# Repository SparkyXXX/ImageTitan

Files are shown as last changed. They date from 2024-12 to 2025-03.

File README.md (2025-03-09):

# 环视采图车使用说明

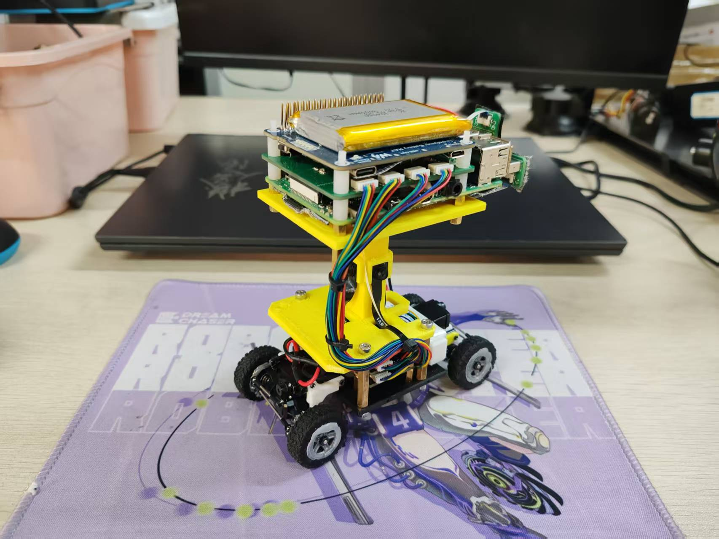
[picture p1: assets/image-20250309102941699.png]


图采车配合手柄、无线键鼠（其实无线键盘就可以）和显示器使用，前者用于操控小车，后者用于启动程序或调试处理异常状况。（如果希望更方便一些省去键鼠也可以在ubuntu上配置自启动）

## 使用步骤

1. 给树莓派插入无线键鼠和手柄的USB接收端，连接好显示器，将手柄开机。

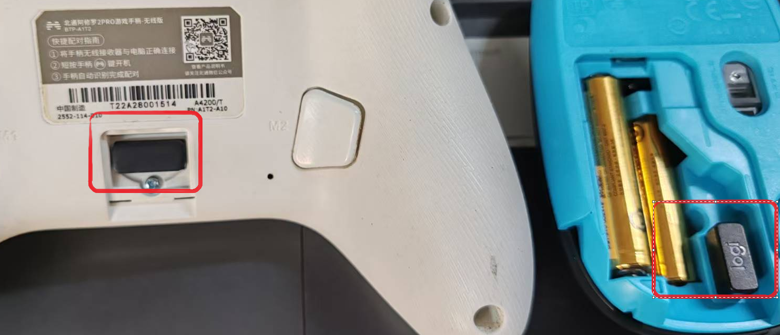
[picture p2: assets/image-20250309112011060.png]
    

2. 按此按钮给树莓派上电

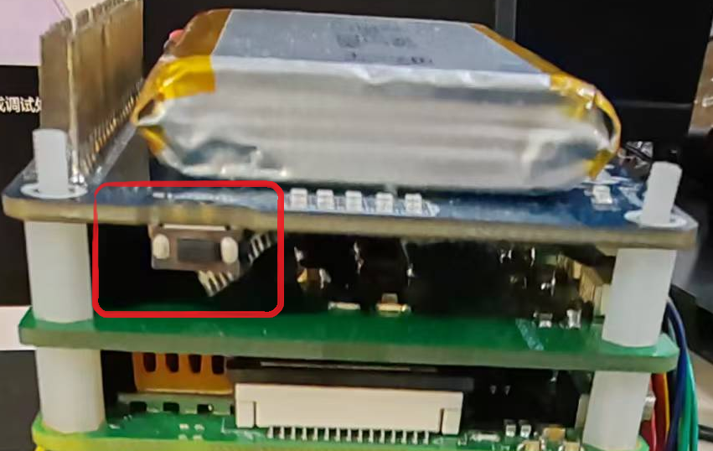
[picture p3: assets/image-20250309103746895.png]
    

3. 插入下位机电池，拨动此开关给单片机上电，此时舵机会回正

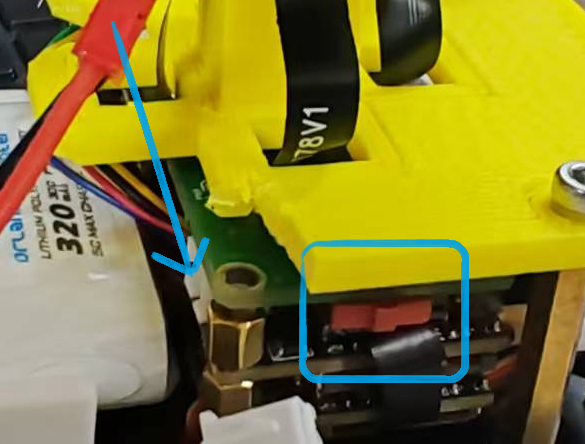
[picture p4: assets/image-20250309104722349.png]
    

4. ctrl+alt+t打开终端，输入以下命令并回车（注：开机登陆密码为英文小写lamps）

    ```shell
    ./all_boot.sh
    ```

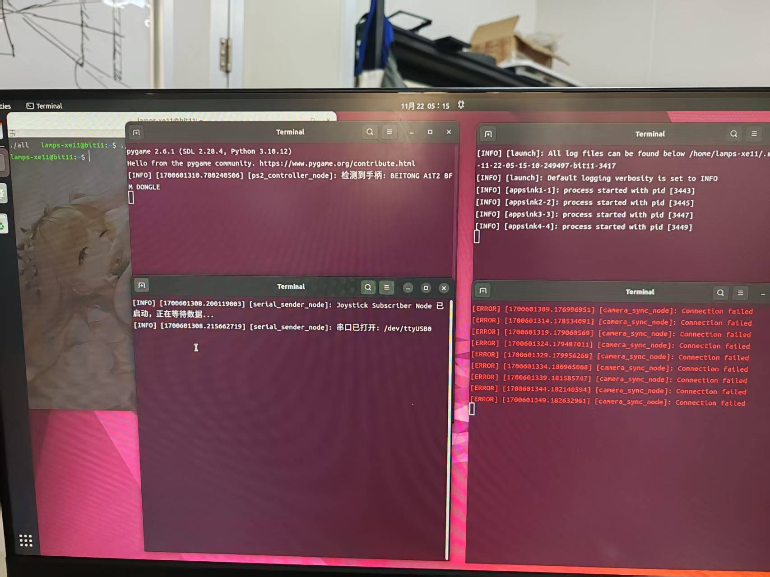
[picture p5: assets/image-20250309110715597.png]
	图中为程序运行的正常界面（注：右下终端的报错来自于已弃用的网络传输功能，忽略即可）

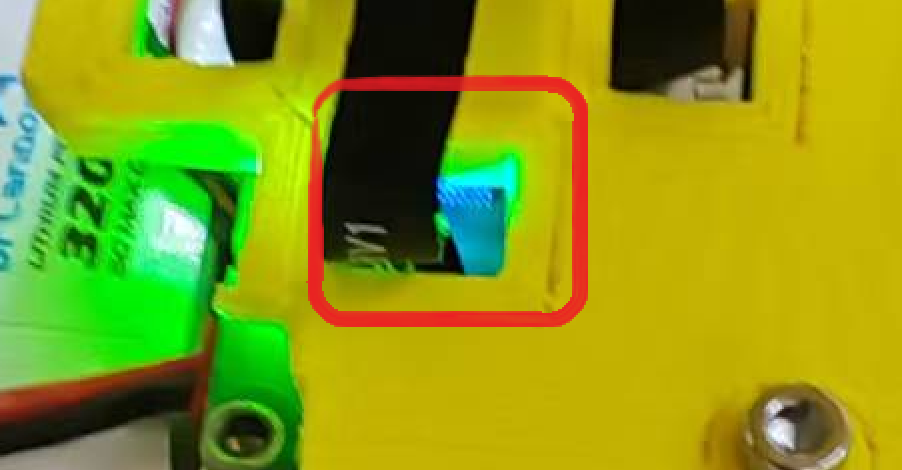
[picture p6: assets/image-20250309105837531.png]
	通过打印件的孔看到微微蓝光，表示程序开始运行

5. 手柄左侧遥控控制车辆移动，右侧A键控制采图开始或结束（按一下切换状态）

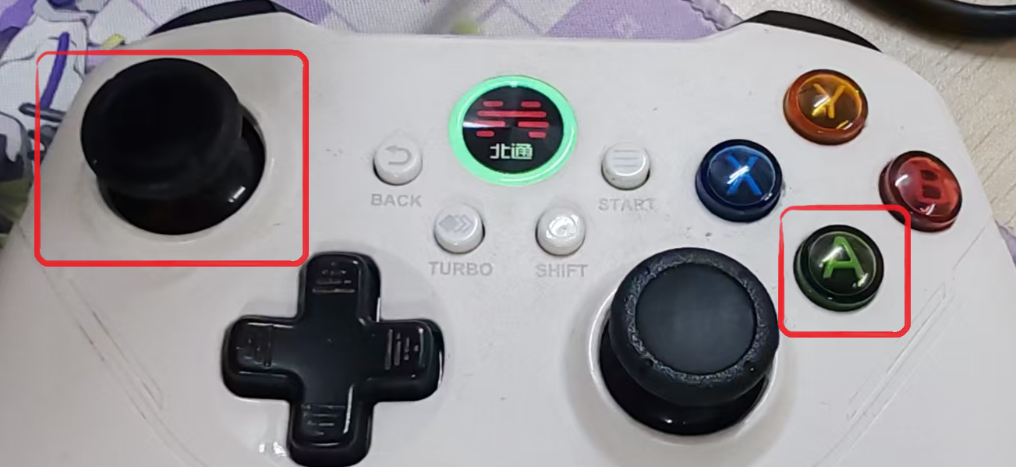
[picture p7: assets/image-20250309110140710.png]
    

6. 拔掉显示器，将车放入场地后，按下A键开始采图，此时第四步中提到的微微蓝光熄灭（注：本来是有红光亮起的，但由于设计考虑不周，被打印件挡住了）

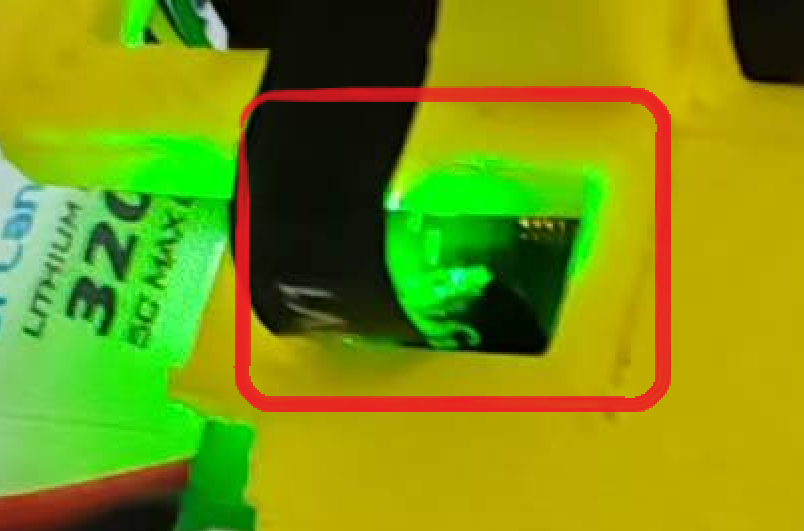
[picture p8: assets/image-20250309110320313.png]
    

7. 手柄控制小车移动以采集图像数据，为了保证图像质量，小车移速设置得较慢，请耐心等待
8. 完成采图后，再次按A键结束采图，此时微微蓝光亮起
9. 连接显示屏，用U盘将home路径下image目录拷贝出来即可（注：请耐心等待进度条走完，点击弹出U盘后，稍等片刻后再拔出U盘，热插拔容易导致数据丢失，且建议在关闭设备前用自己电脑确认U盘中是否确实成功拷出了数据）
10. 确认成功拷出数据后，结束程序，先短按后长按第2步中的按钮，拨动第3步中的按钮，完成下电；并拔出下位机电池

## 注意事项

1. 下位机电池使用后一定记得拔出，长期插着及其不开开关，电池的漏电也会损耗电池寿命，并且存在安全隐患。另外，长时间未使用发现下位机无法正常启动（比如上位机程序检测不到串口，板子指示灯绿光微弱，舵机无力等现象）可以先尝试更换电池。
2. 采图尽快完成，相机发热严重，图像噪声明显增加，且长时间开启会软化PLA打印件，树莓派平台部分可能产生倾斜使车体重心偏移，关机冷却后对打印件产生塑性形变，导致车体容易倾倒，顶层平台进入相机视野等问题。
3. 如果需要定制相机位置，可修改/Components目录下相机台的SW文件并重新打印安装。
4. 小车还有很多可以优化和改进的地方，如果需要任何帮助，欢迎联系瑞祥~~

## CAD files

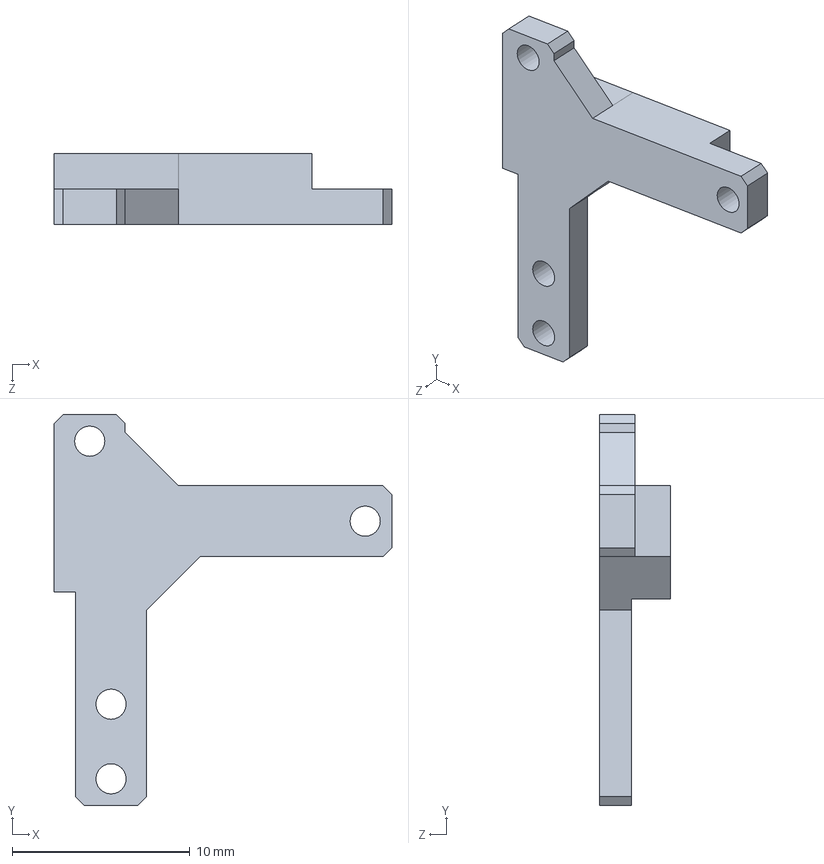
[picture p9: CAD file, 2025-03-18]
Components/前桥连接.SLDPRT
19.0 x 22.0 x 4.00 mm

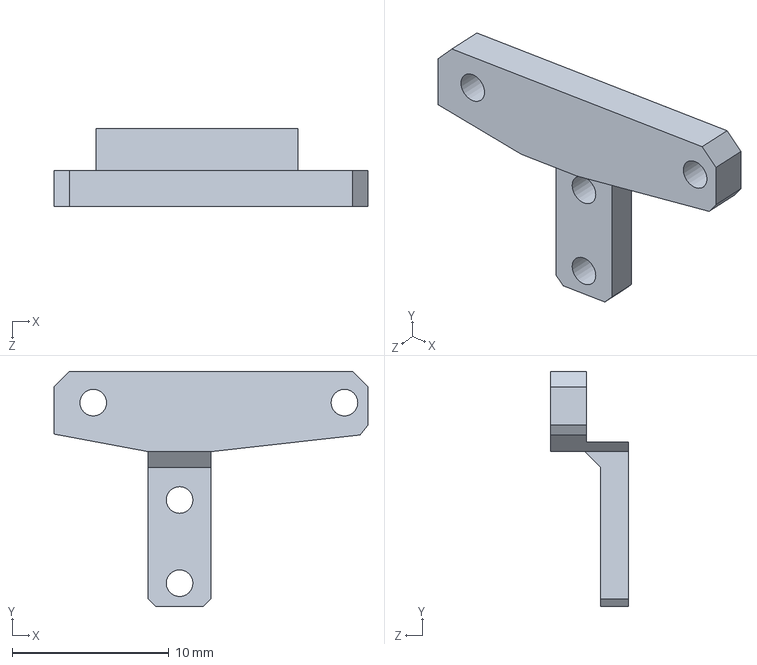
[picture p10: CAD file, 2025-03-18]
Components/后桥连接.SLDPRT
20.0 x 15.0 x 5.00 mm

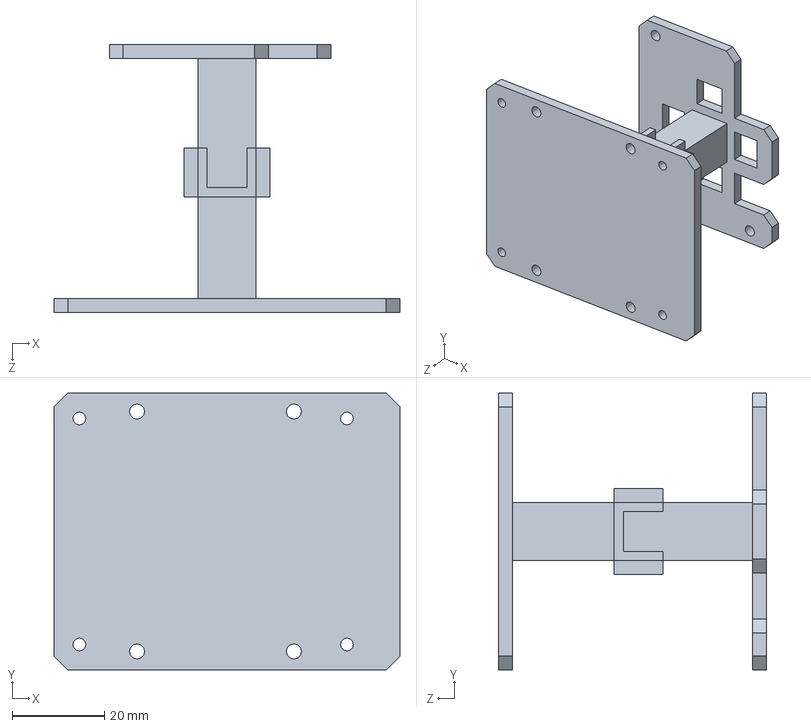
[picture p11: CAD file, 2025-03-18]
Components/相机台.SLDPRT
75.0 x 60.0 x 58.0 mm

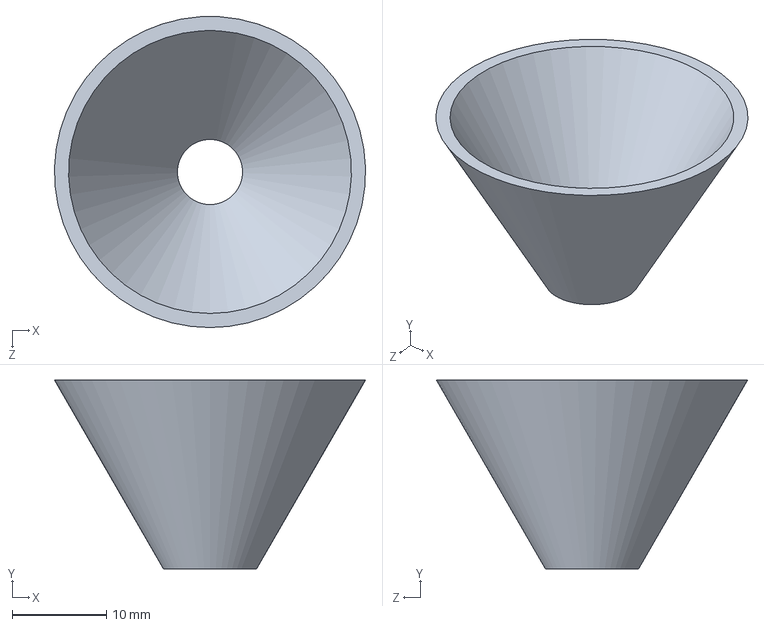
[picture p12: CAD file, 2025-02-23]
Components/视场角模拟.SLDPRT
33.0 x 20.0 x 33.0 mm

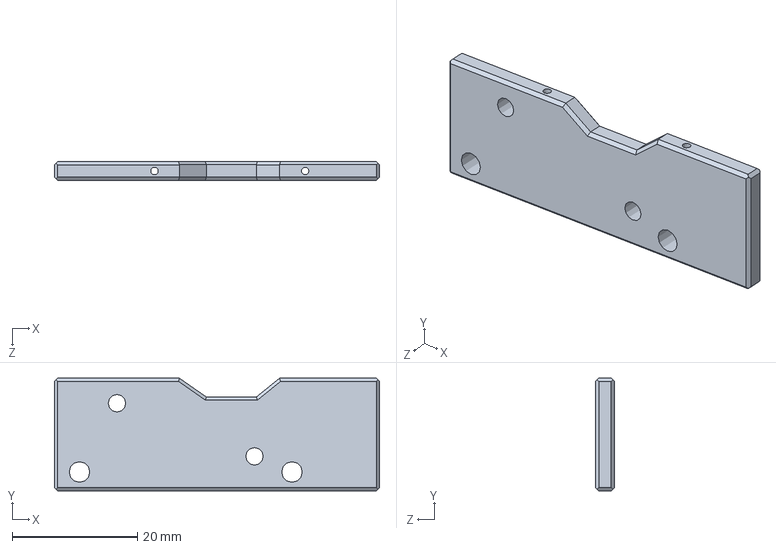
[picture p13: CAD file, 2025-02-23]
Components/生根板.SLDPRT
52.0 x 18.0 x 3.00 mm

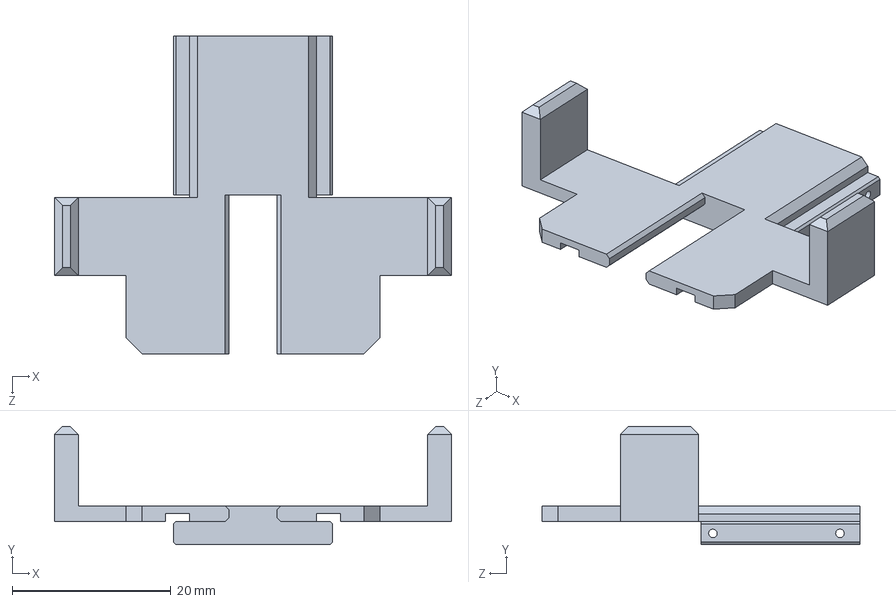
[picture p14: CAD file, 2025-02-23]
Components/电池仓与舵机放置.SLDPRT
50.0 x 14.9 x 40.0 mm

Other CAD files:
Components/前桥连接mirror.SLDPRT
Components/后桥连接mirror.SLDPRT

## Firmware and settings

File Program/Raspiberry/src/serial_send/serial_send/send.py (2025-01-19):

#!/usr/bin/env python3
# -*- coding: utf-8 -*-

import rclpy
from rclpy.node import Node
from sensor_msgs.msg import Joy
from std_msgs.msg import Bool
import serial
import struct

class SerialSenderNode(Node):
    def __init__(self):
        super().__init__('serial_sender_node')
        
        self.subscription = self.create_subscription(Joy, 'joy', self.joy_callback, 10)
        self.get_logger().info("Joystick Subscriber Node 已启动，正在等待数据...")
        self.serial_port = serial.Serial('/dev/ttyUSB0', 115200, timeout=1)
        self.get_logger().info("串口已打开: /dev/ttyUSB0")

        # 初始化 pc_flag 和 img_flag
        self.pc_flag = False
        self.img_flag = False
        self.pc_flag_subscriber = self.create_subscription(Bool, 'pc_flag', self.pc_flag_callback, 10)
        self.img_flag_subscriber = self.create_subscription(Bool, 'img_flag', self.img_flag_callback, 10)

    def pc_flag_callback(self, msg):
        self.pc_flag = msg.data

    def img_flag_callback(self, msg):
        self.img_flag = msg.data

    def joy_callback(self, joy_msg):
        vel = joy_msg.axes[1]
        ang = joy_msg.axes[0]
        self.send_to_serial(vel, ang)

    def send_to_serial(self, vel, ang):
        header = 0xA5
        vel_bytes = struct.pack('<f', vel)  # 使用小端序存储 float
        ang_bytes = struct.pack('<f', ang)  # 使用小端序存储 float
        control_mode = 1  # 假设 control_mode 为 1
        flags = (self.pc_flag << 7) | (self.img_flag << 6) | (control_mode << 5)
        footer = 0x5A
        data = bytes([header]) + vel_bytes + ang_bytes + bytes([flags]) + bytes([footer])
        self.serial_port.write(data)

    def destroy_node(self):
        self.serial_port.close()
        self.get_logger().info("串口已关闭")
        super().destroy_node()

def main(args=None):
    rclpy.init(args=args)
    node = SerialSenderNode()

    try:
        rclpy.spin(node)
    except KeyboardInterrupt:
        pass
    finally:
        node.destroy_node()
        rclpy.shutdown()

if __name__ == '__main__':
    main()

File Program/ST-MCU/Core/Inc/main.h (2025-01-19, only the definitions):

#define IMG_Pin GPIO_PIN_4
#define IMG_GPIO_Port GPIOA
#define PC_Pin GPIO_PIN_5
#define PC_GPIO_Port GPIOA
#define AIN2_Pin GPIO_PIN_12
#define AIN2_GPIO_Port GPIOB
#define AIN1_Pin GPIO_PIN_13
#define AIN1_GPIO_Port GPIOB
#define PWMA_Pin GPIO_PIN_11
#define PWMA_GPIO_Port GPIOA

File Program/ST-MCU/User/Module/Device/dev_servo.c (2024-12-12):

/*
 * @Author: Hatrix 3113624526@qq.com
 * @LastEditTime: 2024-12-12 13:31:30
 * @Description: PWM舵机驱动
 */

#include "dev_servo.h"

void Servo_Init(Dev_Servo_TypeDef *servo, TIM_HandleTypeDef *htim, uint32_t ch)
{
    servo->htim = htim;
    servo->ch = ch;
    HAL_TIM_PWM_Start(servo->htim, servo->ch);
    Servo_SetAngle(servo, 0.0f);
}

float Servo_GetAngle(Dev_Servo_TypeDef *servo)
{
    return servo->angle;
}

void Servo_SetAngle(Dev_Servo_TypeDef *servo, float angle)
{
    servo->angle = angle;
    int16_t pulse = (int16_t)((angle + 90) / 180 * 100 + 25);
    __HAL_TIM_SET_COMPARE(servo->htim, servo->ch, pulse);
}

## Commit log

2024-10-04 完成上位机部分
2024-10-04 修复电机协议
2024-10-04 完成下位机部分
2024-10-04 添加README说明
2024-10-04 补充md
2024-12-12 完成第一版全部开发
    [34.82mm.SLDPRT, 50mm转向机构杆.SLDPRT, 9克微型数字舵机.SLDPRT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]
2024-12-12 完善README
2024-12-12 加入BOM表
    [BOM.xlsx]
2024-12-13 修改gitignore
2025-02-23 加入PCB和SW零件
    [Chassis.PrjPcb, Chassis.SchDoc, Chassis_V1.PcbDoc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]
2025-03-01 修改零件
    [前桥连接.SLDPRT, 前桥连接mirror.SLDPRT, 后桥连接.3mf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]
2025-03-09 添加使用说明
    [Chassis.PrjPcb, Chassis.SchDoc, Chassis_V2.PcbDoc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]
2025-03-09 修正图片路径
2025-03-09 补充开机密码
2025-03-18 调整零件参数
    [前桥连接.SLDPRT, 前桥连接mirror.SLDPRT, 后桥连接.SLDPRT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]

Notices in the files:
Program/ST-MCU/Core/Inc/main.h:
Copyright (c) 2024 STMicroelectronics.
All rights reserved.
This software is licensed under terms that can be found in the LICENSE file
